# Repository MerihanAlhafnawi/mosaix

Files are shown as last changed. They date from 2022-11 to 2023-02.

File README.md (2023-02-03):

# MOSAIX

Thanks for stopping by! You can find anything MOSAIX related on this page.



## What is MOSAIX?

MOSAIX is the first swarm robotic system (completely decentralised) desinged and built to be used by members of the public in large numbers (many robots and many people) to help them in social tasks such as decision-making, brainstorming, art-making and education. MOSAIX is made of individual robots called Tiles. As part of my PhD, I designed and built 100 Tiles. 

## How do I build a Tile?

Building a Tile is simple since most components are off the shelf. Tiles run on a Rasberry Pi 4. However, the base of the Tile is a PCB of our design, and there is one more PCB (the adaprter) that is soldered onto the Raspberry Pi's pins. We also designed some 3D printed components to support the robot, found in [STL files](STL files). The gerber files for both boards can be found in [Base_gerberfiles](Base_gerberfiles) and [Adapter_gerberfiles](Adapter_gerberfiles). The Tile is essentially a stack of the following components:



In order to build a Tile, the following steps need to be taken:
1- Send the PCBs to be manufactured 
2- Obtain off-the-shelf components and solder them onto the base PCB
3- Solder the Adapter PCB onto the Raspberry Pi pins
4- Secure the stack of components using the 3D prints

Here are all the components needed to build a Tile:

1- Raspberry Pi 4 2GB
https://thepihut.com/products/raspberry-pi-4-model-b

2- SD Card 32GB
Any microSD Card for the Raspberry Pi

3- 4-inch LCD touchscreen
https://thepihut.com/products/spi-4-320x480-ips-touch-screen-gpio

4- 4 VL53L0X Time-of-Flight Distance Sensor Carrier with Voltage Regulator, 200cm Max 

5- 10000 mAh power pack 
Any model that is 9.5cm x 6cm x 2cm, with USB A input on the top. 

6- Raspberry Pi Zero camera module 
https://shop.pimoroni.com/products/raspberry-pi-zero-camera-module?variant=37751082058

7- Raspberry Pi Zero camera adapter
https://shop.pimoroni.com/products/camera-cable-adapter?variant=3031293263882

8- 2 Micro metal gearmotor 
https://thepihut.com/products/micro-metal-gearmotor?variant=35654648145

9- Motor brackets 
https://shop.pimoroni.com/products/pololu-micro-metal-gearmotor-bracket-pair-black?variant=471886829

10- TB6612FNG motor driver
https://shop.pimoroni.com/products/sparkfun-motor-driver-dual-tb6612fng-1a-1?variant=2509524533258

11- 2 32mmx7mm Pololu Wheels 
https://shop.pimoroni.com/products/pololu-wheel-32x7mm-pair?variant=390419700

12-  Castor ball
https://www.amazon.co.uk/dp/B083FSLM8Z?psc=1&ref=ppx_pop_dt_b_asin_title

13- 10 Way Flat Ribbon Cable
https://uk.rs-online.com/web/p/ribbon-cable/2899846

14- Molex Right Angle, Through Hole, Plug Type A 2.0 USB Connector
https://uk.rs-online.com/web/p/usb-connectors/8006797

15- Microchip 16-Channel I/O Expander I2C, Serial 28-Pin SOIC, MCP23017-E/SO
https://uk.rs-online.com/web/p/io-expanders/0403816

16- Omron 10-Way Connector Plug for Through Hole Mount, 2-Row
https://uk.rs-online.com/web/p/idc-connectors/2026926

17- ASSMANN WSW 10-Way IDC Connector Socket for Cable Mount, 2-Row
https://uk.rs-online.com/web/p/idc-connectors/6741097

18- PCB Slide Switch Single Pole Double Throw (SPDT) On-Off-On 5 A @ 28 V dc Top
https://uk.rs-online.com/web/p/slide-switches/7347334

19- Molex Straight, SMT, Socket Type B USB Connector
https://uk.rs-online.com/web/p/usb-connectors/8967572

20- USB A to USB micro cable
Any cable

The following are components soldered onto the Base PCB:



As for the 3D components, here is an image explaining the role of each component: 



A) 4 Holes on each side of the shell for proximity sensors. 
B) 4 screw holes at the bottom corners of the shell to screw in the base PCB. 
C) An opening that exposes the USB-C input socket of the power pack in order to charge the robot without opening the case. 
D) A "pocket" that has a hole where the camera is placed, and secured in place by the small shelf in shown in E). 
E) Camera shelf.
F) This part is placed between the touchscreen and the Raspberry Pi and hooks onto the Ethernet port to help level the touchscreen. It can been seen in image A) of the next figure . 
G) This part is glued onto the side of the power pack to help keep it in place since the power pack is narrower than the case. This part can be seen in image C) of the next figure.

We made the cable that connects the power bank to the USB micro connector on the base board by getting a USB A to USB micro cable, cutting it, getting rid of the USB A side, and soldering the VCC and ground wires to the USB connector. The cable can be seen in image C) of the next figure.

After soldering components onto the base PCB, soldering the Adapter PCB onto the pins of the Raspberry Pi, and 3D printing, assembly goes as follows:



Assembly all done!

## How do Tiles communicate?

Since MOSAIX was built to be a decentralised system, I've created a WiFi ad-hoc network to run among the robots so we can avoid any central points of failure (for example, by avoiding using a router). This type of network acts as a plug-and-play feature, where as soon as any of the Raspberry Pis are turned on, the network becomes live (no need to do any extra steps). This means that the swarm can operate and communicate independent of location or internet access. Also, you can connect your laptop/phone to the network to coommunicate with the robots (add a password if you're worried about malicious activity). The network has been quite reliable so far, and I tested it with 65+ robots with no issues. I also have a centralised network for when I want to update the code running on the robots. I can easily switch between those 2 networks (please note I am running the Debian 64-bit Bullseye Operating System). 

First, I set up the ad-hoc network by editing the network interfaces which is found in /etc/network/interfaces. The following snippet is an example of the ad-hoc network settings added to get the network up and running on the Raspberry Pi.

```
iface wlan0 inet static
address 10.2.1.1
netmask 255.255.255.0
wireless-channel 1
wireless-essid mosaix
wireless-mode ad-hoc
```

In order to switch between ad-hoc and centralised WiFi, I trigger a shell command to replace the "wpa_supplicant.conf" file wither to the ad-hoc or to the central WiFi configurations. Both files can be found in [code](code). More on how this is done is under "How do I program Tiles?".

Bluetooth is another option, however, I found it to be unreliable so I do not use it often.

## How do I program Tiles?

They run on Rasberry Pis so sky is the limit!! However, to make my life easier, I have a system I developed in order to update code on the entire swarm of Tiles, turn them off all at once, etc. Here is what I do (DISCLAIMER: I am not claiming this is the best/most efficient way,
it's just a system that I created and worked for my applications, feel free to adopt and/or develop your own!):

Coming soon

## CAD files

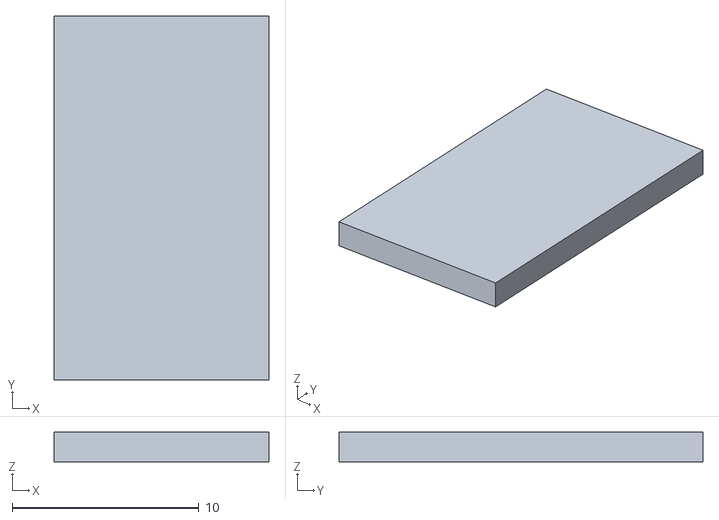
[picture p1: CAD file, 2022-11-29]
STL files/cam_shelf.stl
11.5 x 19.5 x 1.60

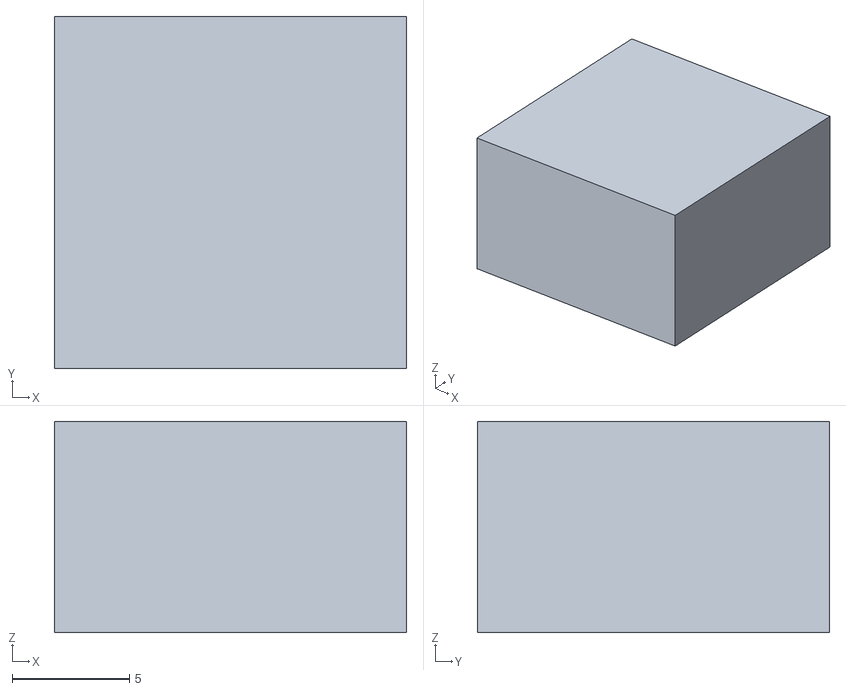
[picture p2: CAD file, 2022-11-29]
STL files/charger_block.stl
15.0 x 15.0 x 9.00

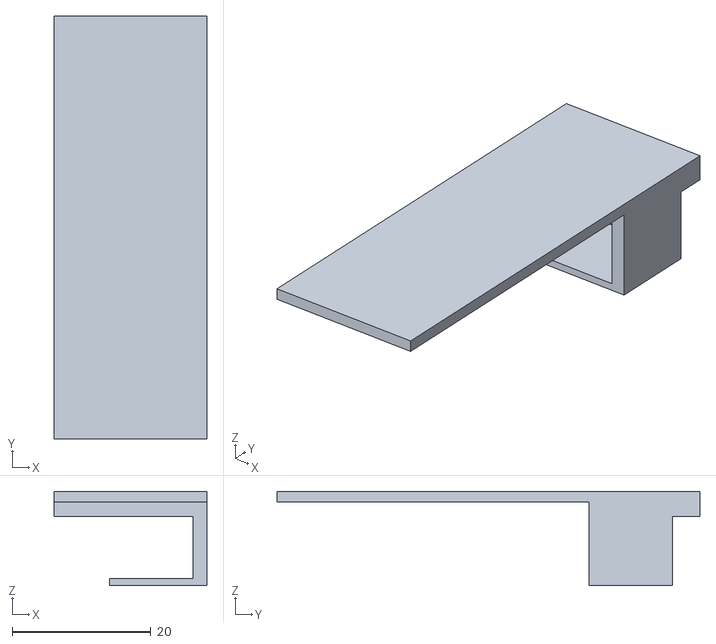
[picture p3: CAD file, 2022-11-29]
STL files/ethport.stl
22.0 x 61.0 x 13.6

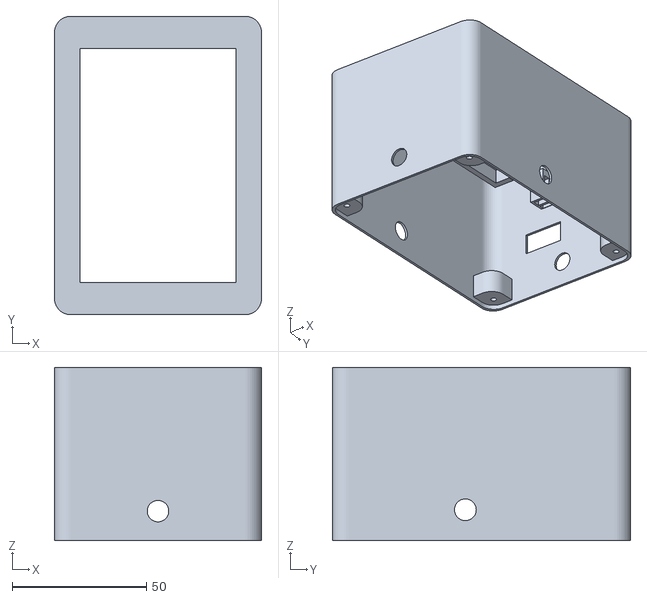
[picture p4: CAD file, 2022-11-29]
STL files/tile_shell.stl
77.0 x 111.0 x 64.5

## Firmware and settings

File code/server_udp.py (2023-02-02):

import socket
import time
import subprocess
import _thread
import json
from csv import writer
import os
import math
from datetime import datetime
filename = ''
started1 = False
started2 = False
server = socket.socket(socket.AF_INET, socket.SOCK_DGRAM, socket.IPPROTO_UDP)

# Enable port reusage so we will be able to run multiple clients and servers on single (host, port). 
# Do not use socket.SO_REUSEADDR except you using linux(kernel<3.9): goto https://stackoverflow.com/questions/14388706/how-do-so-reuseaddr-and-so-reuseport-differ for more information.
# For linux hosts all sockets that want to share the same address and port combination must belong to processes that share the same effective user ID!
# So, on linux(kernel>=3.9) you have to run multiple servers and clients under one user to share the same (host, port).
# Thanks to @stevenreddie


server.setsockopt(socket.SOL_SOCKET, socket.SO_REUSEPORT, 1)

# Enable broadcasting mode
server.setsockopt(socket.SOL_SOCKET, socket.SO_BROADCAST, 1)
server.bind(("", 37021))

started1 = False
started2 = False
neighbourhood = []
send_neighbourhood = ''
op_count= [0]*21 #list containing opinions spaced by 5%
count = 0
filename = os.path.join('robot_logs' + '.csv')
while (os.path.isfile(filename) == True):
   filename = os.path.join('robot_logs' +  str(count) + '.csv')
   count = count + 1
open(filename, 'a').close()
fields =["robot_id", "opinion", "aggregate", "hour", "minute", "second", "comp_hour", "comp_minute", "comp_second"]
with open(filename, 'a+', newline='') as write_obj:
    # Create a writer object from csv modules
    csv_writer = writer(write_obj)
    # Add contents of list as last row in the csv file
    csv_writer.writerow(fields)
print (filename)
def recv_thread(server):
    global neighbourhood
    global send_neighbourhood
    global filename
    while True:
        send_neighbourhood = ''
        found_neighbour = False
        data, addr = server.recvfrom(1024)
        print("message received!", data) 
        decoded = bytes.decode(data, 'utf-8')
        print (neighbourhood)
        rid = ""
        found_neighbour = False
        aggregate = ""
        curr_pos = 0
        opinion = ""
        for i in range (3, len(decoded)):
            if (decoded[i] != 'a'):
                rid += decoded[i]
            else:
                break
            curr_pos = i
        for i in range (curr_pos+2, len(decoded)):
            if (decoded[i] != 'o'):
                aggregate += decoded[i]
            else:
                break
            curr_pos = i
        for i in range (curr_pos+2, len(decoded)):
            if (decoded[i] != ' '):
                opinion += decoded[i]
            else:
                break
            curr_pos = i
        for l in range (len(neighbourhood)):  

            if (neighbourhood[l][0] == rid):
                if (neighbourhood[l][1] != aggregate or neighbourhood[l][2] != opinion):
                    dateTimeObj = datetime.now()
                    h = str(dateTimeObj.hour)
                    m = str(dateTimeObj.minute)
                    s = str(dateTimeObj.second)
                    print ("rid: ", rid, ", opinion: ", opinion, ", aggregate: ", aggregate, "time: ", h, ":", m, ":",s)
                    fields =[rid, aggregate, opinion, h, m,s]
                    with open(filename, 'a+', newline='') as write_obj:
                       # Create a writer object from csv modules
                       csv_writer = writer(write_obj)
                       # Add contents of list as last row in the csv file
                       csv_writer.writerow(fields)
    
                neighbourhood[l][1] = aggregate
                neighbourhood[l][2] = opinion
                found_neighbour = True
                break
        if (found_neighbour == False):
            neighbourhood.append([rid, aggregate, opinion]) 
            dateTimeObj = datetime.now()
            h = str(dateTimeObj.hour)
            m = str(dateTimeObj.minute)
            s = str(dateTimeObj.second)
            print ("rid: ", rid, ", opinion: ", opinion, ", aggregate: ", aggregate, "time: ", h, ":", m, ":",s)
            fields =[rid, aggregate, opinion, h, m,s]
            with open(filename, 'a+', newline='') as write_obj:
               # Create a writer object from csv modules
               csv_writer = writer(write_obj)
               # Add contents of list as last row in the csv file
               csv_writer.writerow(fields)
        print ("rid: ", rid, ", aggregate: ", aggregate, ", opinion: ", opinion)
        print (neighbourhood)
        
        for neighbour in neighbourhood:
            send_neighbourhood += 'rpi' + neighbour[0] + 'a' + neighbour[1] + 'o' + neighbour[2] + '-'
        if (send_neighbourhood[len(send_neighbourhood)-1] == '-'):
             send_neighbourhood = send_neighbourhood[:-1]
        print ("string: ", send_neighbourhood)
        
        
        
        send_text = str.encode(send_neighbourhood, 'utf-8')
#example: b'rid13uid8cond35h1m9s7'
#example: b'rid1uid8cond35h1m9s7'
#rid: robot ID that goes from 1-100
#uid: user ID, can vary depending on application, but it is a number
#cond: condition (or opinion) user has entered
#h,m,s: time in hour, minute and second the condition was entered


print ("Welcome robot witch/wizard...\n")

print ("Here is the order of how to communicate with robots\n")
print ("First, you need to shake hands with the robots, then you need to update the code you want them to run")
print ("then you need to tell them to start running, you can then tell them to stop running and finally, to shut down\n")
print ("How to do this you ask?? Well here is the list:\n")
print ("For shaking hands, type \"handshake\"")
print ("For code update, type \"update\"")
print ("For updating startup code, type \"startup\"")
print ("For running the code, type \"run\"")
print ("For stopping the code, type \"stop\"")
print ("For deleting csv log files on robots, type \"delete\"")
print ("For rebooting, type \"reboot\"")
print ("For shutting down, type \"shutdown\"")

#start a different thread that listens to the robots
_thread.start_new_thread(recv_thread,(server,))
 #need to add: update source code (send_start_up) so we also need to add
 #reboot
 #add run1 and run2 to save on different files
def send_message(message):
    for i in range(10):
        server.sendto(message, ('<broadcast>', 37020))

while True:

    command = input()
    if (command == 'handshake'):
        count = 0
        
        send_message(b"handshake")
        print("Handshake command sent!")

    elif (command == 'update'):   
        send_message(b"update")
        print("Update command sent!")

    elif (command == 'update_directory'):   
        send_message(b"update_directory")
        print("Update command sent!")

    elif (command == 'motors'):   
        send_message(b"motors")
        print("Motors sent")

    elif (command == 'central'):   
        send_message(b"central")
        print("Central sent")

    elif (command == 'adhoc'):   
        send_message(b"adhoc")
        print("Adhoc sent")

    elif (command == 'run' or command == 'run1' or command == 'run2' or command == 'run3' or command == 'run4'):
        send_message(command.encode())
        print("Run command sent!")
        if (started1 == False):
            started1 = True
            count = 1
            

    elif (command == 'stop'):    
        send_message(b"stop")
        started2 = False
        started1 = False
        neighbourhood = []
        print("Stop command sent!")

    elif (command == 'shutdown'):    
        send_message(b"shutdown")
        #server.close()
        print("Shutdown command sent!")
        print ("Mischief managed! Goodbye")
        quit()

    elif (command == 'startup'):
        send_message(b"startup")
        print("Startup command sent!")

    elif (command == 'reboot'):    
        send_message(b"reboot")
        #server.close()
        print("Reboot command sent!")
        print ("Next command should be handshake")

    elif (command == 'delete'):
        send_message(b"delete")
        print("Delete command sent!")

    else:
        print ("This is not a valid command, here is the list again:\n")
        print ("For shaking hands, type \"handshake\"")
        print ("For code update, type \"update\"")
        print ("For updating startup code, type \"startup\"")
        print ("For running the code, type \"run\"")
        print ("For stopping the code, type \"stop\"")
        print ("For deleting csv log files on robots, type \"delete\"")
        print ("For rebooting, type \"reboot\"")
        print ("For shutting down, type \"shutdown\"")

       
    command = ''




    

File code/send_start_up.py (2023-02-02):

from guizero import *   
import tkinter as tk
import tkinter.font as font
import socket
import subprocess
import ipaddress
import RPi.GPIO as GPIO
import urllib.request
import sys
import board
import _thread
import busio
from digitalio import Direction, Pull
from adafruit_mcp230xx.mcp23017 import MCP23017
import adafruit_vl53l0x
import os
from time import sleep
from motors import *


i2c = busio.I2C(board.SCL, board.SDA)


mcp = MCP23017(i2c) # initialized port extender




##### Set xshut pin directions and levels #####

enable0 = mcp.get_pin(0)
enable0.pull = Pull.UP
enable0.direction = Direction.OUTPUT
enable0.value = False
   
enable1 = mcp.get_pin(1)
enable1.pull = Pull.UP
enable1.direction = Direction.OUTPUT
enable1.value = False
    
enable2 = mcp.get_pin(2)
enable2.pull = Pull.UP
enable2.direction = Direction.OUTPUT
enable2.value = False
    
enable3 = mcp.get_pin(3)
enable3.pull = Pull.UP
enable3.direction = Direction.OUTPUT
enable3.value = False
    
    
##### enable one sensor after the other by setting xshut pins high one after the oter and set new addresses
sensors_functioning = [True, True, True, True]
try:
    enable0.value = True
    ToF0 = adafruit_vl53l0x.VL53L0X(i2c)
    ToF0.set_address(0x30)
except:
    sensors_functioning[0] = False
    print ("Right sensor not working")
    backgrd = "red"

try:
    enable1.value = True
    ToF1 = adafruit_vl53l0x.VL53L0X(i2c)
    ToF1.set_address(0x31)
except:
    sensors_functioning[1] = False
    print ("Front sensor not working")
    backgrd = "red"

try:
    enable2.value = True
    ToF2 = adafruit_vl53l0x.VL53L0X(i2c)
    ToF2.set_address(0x32)
except:
    sensors_functioning[2] = False
    print ("Back sensor not working")
    backgrd = "red"

try:
    enable3.value = True
    ToF3 = adafruit_vl53l0x.VL53L0X(i2c)
    ToF3.set_address(0x33)
except:
    sensors_functioning[3] = False
    print ("Left sensor not working")
    backgrd = "red" 

#### set output pins for motor drivers 

in1 = mcp.get_pin(9)
in1.pull = Pull.UP
in1.direction = Direction.OUTPUT
in1.value = False

in2 = mcp.get_pin(8)
in2.pull = Pull.UP
in2.direction = Direction.OUTPUT
in2.value = False

in3 = mcp.get_pin(11)
in3.pull = Pull.UP
in3.direction = Direction.OUTPUT
in3.value = False

in4 = mcp.get_pin(12)
in4.pull = Pull.UP
in4.direction = Direction.OUTPUT
in4.value = False

stby = mcp.get_pin(10)
stby.pull = Pull.UP
stby.direction = Direction.OUTPUT
stby.value = True

en = 5
en2 = 6

temp1=0
GPIO.setmode(GPIO.BCM)

GPIO.setup(en,GPIO.OUT)
GPIO.setup(en2,GPIO.OUT)

p_val=GPIO.PWM(en,1000)
p2_val = GPIO.PWM(en2,1000)
p_val.start(50)
p2_val.start(50)
p_val.ChangeDutyCycle(50)
p2_val.ChangeDutyCycle(50)

start_time = 0
stby.value = True
def move(direction):
        i1, i2, i3, i4 = dir(direction)
        in1.value = i1
        in2.value = i2
        in3.value = i3
        in4.value = i4

client = socket.socket(socket.AF_INET, socket.SOCK_DGRAM, socket.IPPROTO_UDP) # UDP

rasp_id = socket.gethostname()
robot_id = rasp_id[11:len(rasp_id)]

# Enable port reusage so we will be able to run multiple clients and servers on single (host, port). 
# Do not use socket.SO_REUSEADDR except you using linux(kernel<3.9): goto https://stackoverflow.com/questions/14388706/how-do-so-reuseaddr-and-so-reuseport-differ for more information.
# For linux hosts all sockets that want to share the same address and port combination must belong to processes that share the same effective user ID!
# So, on linux(kernel>=3.9) you have to run multiple servers and clients under one user to share the same (host, port).
# Thanks to @stevenreddie
client.setsockopt(socket.SOL_SOCKET, socket.SO_REUSEPORT, 1)

# Enable broadcasting mode
client.setsockopt(socket.SOL_SOCKET, socket.SO_BROADCAST, 1)

client.bind(("", 37020))


data = 'none'
p = None 
data = None
addr = None
started1 = False
started2 = False
last_message = ''
curr_message = ''

text_append = ''
backgrd = "bisque"

def run_code():
    global backgrd, last_message, started1, p, addr, data, start_text
    if (started1 == False):
        print ("starting")
        backgrd = run_code_btn_colour

        start_text.value = "Starting now \n please wait"
        #send the ip address and port as arguments when running python code 
        p = subprocess.Popen(["python3", "/home/pi/Desktop/code.py"]) 
        started1 = True
        
    last_message = 'run1'

def update_code():
    global backgrd, last_message, started1, p, addr, data, start_text
    try:
       url = 'http://' + addr[0] + ':8000/code.py'
       urllib.request.urlretrieve(url, '/home/pi/Desktop/code.py')
       start_text.value = "Code updated"
       print ("updated code")
       backgrd = fetch_code_btn_colour
    except: 
        start_text.value = "Did not update. \n Send a handshake \n command from \n server_udp.py from \n computer so the robot \n knows the addr"
        print ("Need to handshake first")
        backgrd = "red"
    
    last_message = 'update'

def startup():
    global backgrd, last_message, started1, p, addr, data, start_text
    try: 
        url = 'http://' + addr[0] + ':8000/send_start_up.py'
        urllib.request.urlretrieve(url, '/home/pi/Desktop/send_start_up.py')
        backgrd = fetch_startup_btn_colour
        print ("updated startup")
        start_text.value = "Startup code udpated"
    except:
        start_text.value = "Did not update. \n Send a handshake \n command from \n server_udp.py from \n computer so the robot \n knows the addr"
        print ("Need to handshake first")
        backgrd = "red"

    last_message = 'startup'

def central():
    global backgrd, last_message, started1, p, addr, data, start_text
    last_message = 'central'
    backgrd = connect_central_btn_colour
    print ("switched to central")
    subprocess.call ("sudo cp /home/pi/Desktop/central.conf /etc/wpa_supplicant/wpa_supplicant.conf", shell = True)
    start_text.value = "Switched to Central \n SSID: SwarmTouch \n Now reboot \n \n WARNING: it takes some \n time to find and \n connect to the network \n so be patient \n upon reboot"

def adhoc():
    global backgrd, last_message, started1, p, addr, data, start_text
    last_message = 'adhoc'
    backgrd = connect_adhoc_btn_colour
    print ("switched to adhoc")
    subprocess.call ("sudo cp /home/pi/Desktop/adhoc.conf /etc/wpa_supplicant/wpa_supplicant.conf", shell = True)
    start_text.value = "Switched to Adhoc \n SSID: mosaix \n Now reboot"

def shutdown():
    subprocess.call("sudo poweroff", shell=True)

def reboot():
    subprocess.call("sudo reboot", shell=True)
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
